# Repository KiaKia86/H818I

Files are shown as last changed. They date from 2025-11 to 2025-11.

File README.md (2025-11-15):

# *H818I*

### A high-performance custom rocket designed entirely from scratch, using a 4-layer avionics PCB, custom airframe, and custom solid motor. The rocket is expected to reach **6,000 ft (≈1,829 m)** at **Mach 0.6**, powered by a **385 N thrust** motor.

### The airframe is constructed with lightweight composite sections reinforced with fiberglass cloth and resin. The rocket includes 2 pyro channels, offering flexibility for multiple deployments and different control configurations.

### The avionics is built on a **4-layer PCB** with one microcontrollers — a **ESP32-S3** — working to process flight data and transmit telemetry via **LoRa** to the ground station. The board includes multiple sensors to track acceleration, rotation, altitude, and GPS position.



---

# Bill of Materials (BOM)

| **Category** | **Item** | **Details** | **Est. Price** | **Purchase Link** |
|---|---|---|---|---|
| Structure | Fiberglass Cloth (6oz) | $21.99 |  | https://www.amazon.com/Fiberglass-Fabric-Glass-Repair-Surfboard/dp/B0DN5FFPSV |
| Structure | Fiberglass Cloth (4oz) | $42.99 |  | https://www.amazon.com/YIQUEDOK-Fiberglass-48-75-Sq-Ft-Surfboard-Repair/dp/B0F74917P7 |
| Structure | Econostitch Peel (5 yards) | $29.95 |  | https://www.amazon.com/Fibre-Glast-Econostitch-Package-Visible/dp/B07DP3PNPJ |
| Structure | TotalBoat 5:1 Marine Epoxy | $159.99 |  | https://www.amazon.com/TotalBoat-Epoxy-Quart-Fast-Hardener/dp/B00HR85152 |
| Structure | Primer | $7.97 |  | https://www.amazon.com/Rust-Oleum-Automotive-260510-12-Ounce-Sandable/dp/B006ZLQ4HQ |
| Structure | Paint | $6.19 |  | https://www.amazon.com/Rust-Oleum-249127-Painters-Purpose-12-Ounce/dp/B002BWOS7Q |
| Structure | Plastic Drop Cloth | $9.47 |  | https://www.amazon.com/Plastic-Drop-Cloths-6-Pack-Disposable/dp/B0DQDWV1SV |
| Structure | Parachute (36 inch) | $18.69 |  | https://www.apogeerockets.com/Building-Supplies/Parachutes/Larger-than-24in/36in-Printed-Nylon-Parachute/Review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 |
| Structure | Kevlar Shock Cord | $40.69 |  | https://www.apogeerockets.com/Building-Supplies/Shock-Cord/Kevlar-Shock-Cord-4500-20-feet-long-3-loops |
| Avionics |PCBA Shipping Cost | $42.22 |  | N/A Custom Quote |

**Total Estimated Cost: $380.15

**Note:**
The PCB cost is not included in the bom, as it is funded by an external source (JLCPCB). Filament and other materials on hand are not considered either!

---

### PCB Overview

The **4-layer PCB** serves as the core of the H818I flight computer.  
It uses:
- **ESP32-S3** (Telemetry, communication, logging, and sensor data)  
- **LoRa radio module** for long-range ground communication  
- Multiple onboard sensors: **IMU**, **barometer**, **magnetometer**, **GPS**, and **accelerometer**  
- **Two pyro channels** for deployment   

The avionics system is designed for flexibility, allowing reuse across future rocket designs.




---

### Why Did I Make This Rocket?

I've wanted to design something that combines all of my passions into one project, and this is it. H818I represents months of hard work, simulation, and testing. Everything I learned about propulsion, control, and flight dynamics has been combined into a single rocket! 

---

# Physical Build
Coming soon!

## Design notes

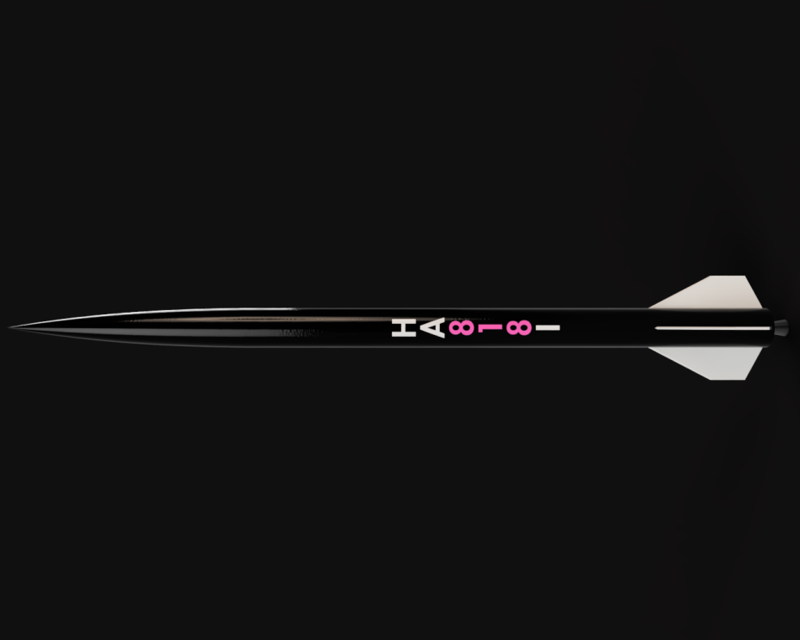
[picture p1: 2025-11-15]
Images/CAD/MainSide1 (1).png

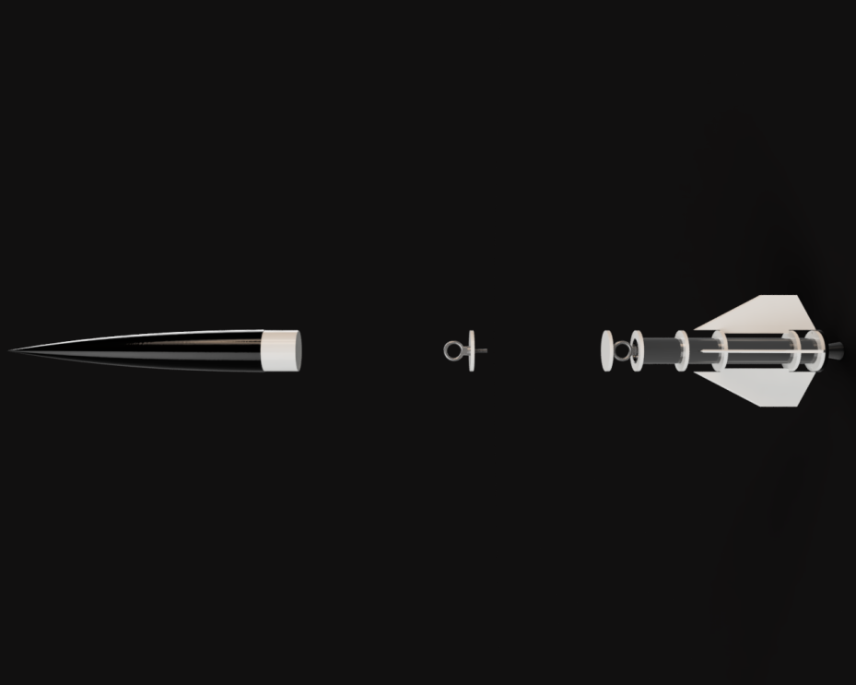
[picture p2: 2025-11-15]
Images/CAD/MainSide2 (1).png

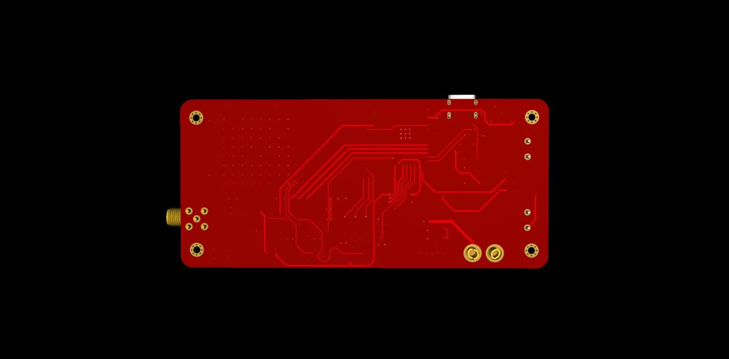
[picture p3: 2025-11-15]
Images/PCB/Screenshot_2025-11-01_200118.png

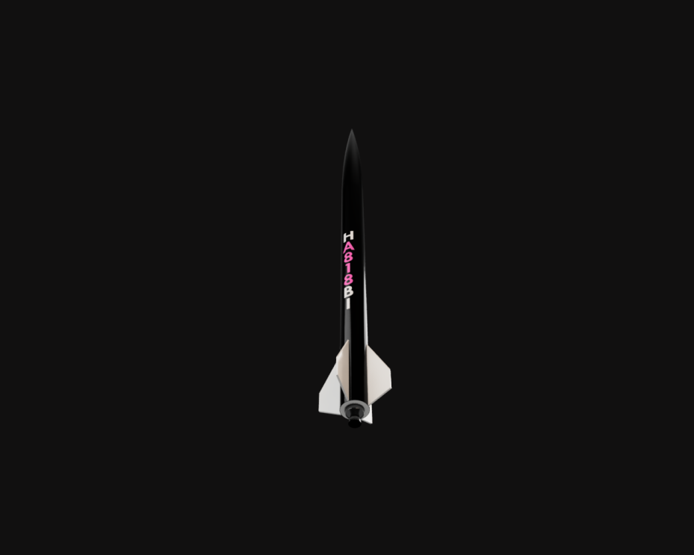
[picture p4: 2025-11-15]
Images/CAD/MainBottomView (1).png

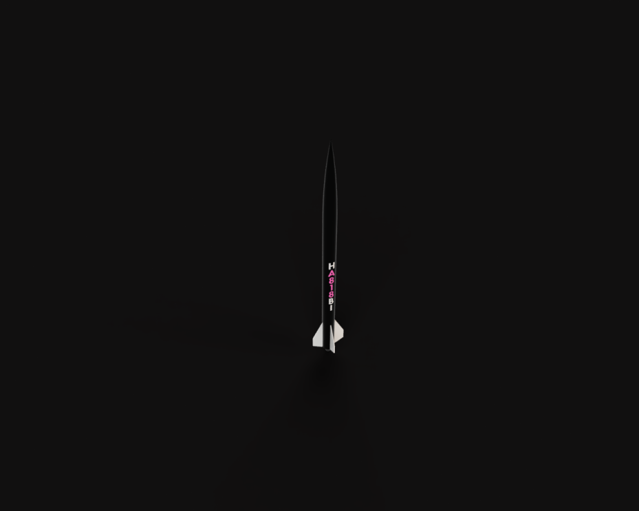
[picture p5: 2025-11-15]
Images/CAD/MainNearView (1).png

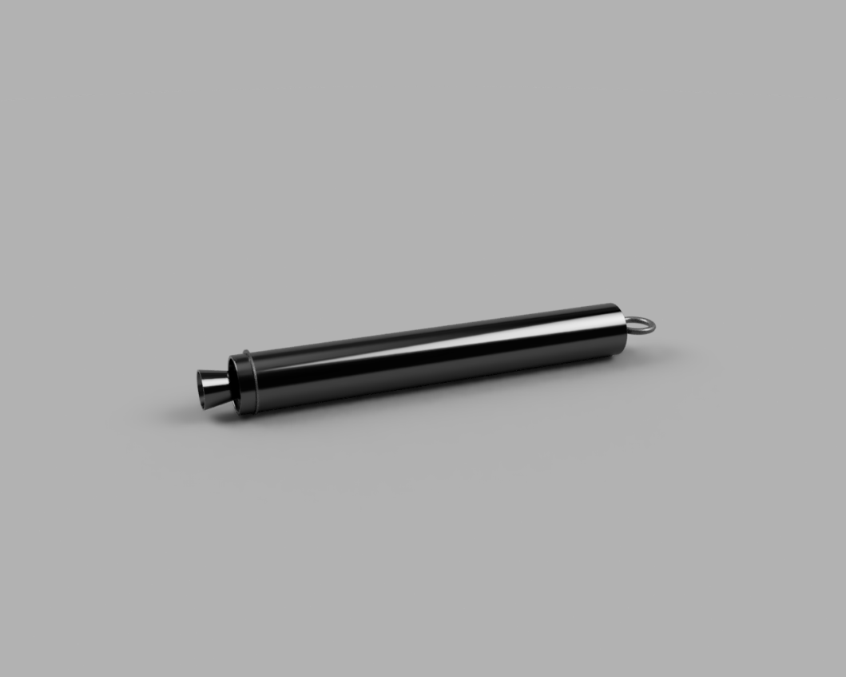
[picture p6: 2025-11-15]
Images/CAD/MainSideRender (1).png

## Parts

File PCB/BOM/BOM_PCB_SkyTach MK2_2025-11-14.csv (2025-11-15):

ID | Name | Designator | Footprint | Quantity | Manufacturer Part | Manufacturer | Supplier | Supplier Part | Price | Pins | 3DModel | Contributor | JLCPCB Part Class | description | license | link
1 | 100nF | C1,C2,C4,C6,C13,C17,C18,C19,C20,C21,C22,C24,C25,C27,C28,C29,C30,C31,C32 | C0603 | 19 | GRM188R71C104KA01D | muRata(村田) | LCSC | C45000 | 0.008 | 2 | C0603_L1.6-W0.8-H0.8 | lcsc | Extended Part |  |  | https://item.szlcsc.com/362304.html
2 | 100nF | C3 | C0603 | 1 | CL10B104KB8NNNC | SAMSUNG(三星) | LCSC | C1591 | 0.003 | 2 | C0603_L1.6-W0.8-H0.8 | lcsc | Extended Part |  |  | https://item.szlcsc.com/362304.html
3 | 1uF | C5 | C0603 | 1 | CL10A105KO8NNNC | SAMSUNG(三星) | LCSC | C1592 | 0.003 | 2 | C0603_L1.6-W0.8-H0.8 | lcsc | Extended Part |  |  | https://item.szlcsc.com/362304.html
4 | 470nF | C12,C15 | C0603 | 2 | GRM188R71A474KA61D | muRata(村田) | LCSC | C435402 | 0.026 | 2 | C0603_L1.6-W0.8-H0.8 | LCSC | Extended Part |  |  | https://item.szlcsc.com/362304.html
5 | 10uF | C23 | C0603 | 1 | C1608X5R1E106MT000E | TDK | LCSC | C76614 | 0.047 | 2 | C0603_L1.6-W0.8-H0.8 | LCSC | Extended Part |  |  | https://item.szlcsc.com/362304.html
6 | 22uF | C7,C8,C9,C10,C11 | C0805 | 5 | GRM21BR61E226ME44L | muRata(村田) | LCSC | C86816 | 0.041 | 2 | C0805_L2.0-W1.3-H1.3 | lcsc | Extended Part |  |  | https://item.szlcsc.com/373011.html
7 | 10uF | C14,C16 | C0805 | 2 | GRM21BR61H106KE43L | muRata(村田) | LCSC | C440198 | 0.063 | 2 | C0805_L2.0-W1.3-H1.3 | LCSC | Basic Part |  |  | https://item.szlcsc.com/373011.html
8 | 1uF | C26 | C0805 | 1 | CL21B105KOFNNNE | SAMSUNG(三星) | LCSC | C24123 | 0.01 | 2 | C0805_L2.0-W1.3-H1.3 | lcsc | Extended Part |  |  | https://item.szlcsc.com/373011.html
9 | TVS | D1,D2,D3 | SOD-523_L1.2-W0.8-LS1.6-BI | 3 | LESD5D5.0CT1G | LRC(乐山无线电) | LCSC | C383211 | 0.021 | 2 | SOD-523_L1.2-W0.8-LS1.6-BI | LCSC | Extended Part |  |  | https://lcsc.com/product-detail/TVS_ESD5Z5V0C_C129211.html
10 | U.FL-R-SMT-1(80) | JP1 | RF-SMD_FRF05002-JSS103M | 1 | U.FL-R-SMT-1(80) | HRS(广濑) | LCSC | C88374 | 0.132 | 3 | RF-SMD_FRF05002-JSS103M | lcsc | Extended Part |  |  | https://atta.szlcsc.com/upload/public/pdf/source/20210518/C2834409_AD8449F4C312B9B9971CC712CA9E2040.pdf
11 | 2.7uH | L1 | IND-SMD_L7.5-W7.5_XAL7030 | 1 | XAL7030-272MEC | Coilcraft(线艺) | LCSC | C5366402 | 1.994 | 2 | IND-SMD_L7.5-W7.5_XAL7030 | lcsc | Extended Part |  |  | https://www.mouser.com/datasheet/2/597/xal7030-270749.pdf
12 | FC-2012HRK-620D | POW | LED0805-R-RD | 1 | NCD0805R1 | 国星光电 | LCSC | C84256 | 0.012 | 2 | LED0805-RD | lcsc | Basic Part |  |  | https://item.szlcsc.com/88042.html
13 | GL | LED2,LED3,LED4 | LED0603-RD | 3 | 19-217/GHC-YR1S2/3T | EVERLIGHT(亿光) | LCSC | C72043 | 0.019 | 2 | LED0603-RD | lcsc | Extended Part |  |  | https://item.szlcsc.com/347874.html
14 | WJ127-5.0-2P | PYRO1,PYRO2 | CONN-TH_2P-P5.00_CPC3703CTR | 2 | WJ127-5.0-2P | KANGNEX(康奈克斯电气) | LCSC | C3703 | 0.129 | 2 | CONN-TH_2P-P5.00_CPC3703CTR | lcsc | Extended Part |  |  | https://item.szlcsc.com/98720.html
15 | SI7232DN-T1-GE3 | Q1 | POWER-1212-8_L3.3-W3.3-P0.66-LS3.3-BL | 1 | SI7232DN-T1-GE3 | VISHAY(威世) | LCSC | C144854 | 0.756 | 10 | POWER-1212-8_L3.3-W3.3-P0.66-LS3.3-BL | LCSC | Extended Part |  |  | https://item.szlcsc.com/152942.html
16 | 10kΩ | R1,R2,R5,R7,R8 | R0603 | 5 | 0603WAJ0103T5E | UNI-ROYAL(厚声) | LCSC | C15401 | 0.001 | 2 | R0603 | lcsc | Extended Part |  |  | https://www.mouser.in/datasheet/2/447/PYu_RT_1_to_0_01_RoHS_L_11-1669912.pdf
17 | 100kΩ | R3 | R0603 | 1 | RC0603FR-07100KL | YAGEO(国巨) | LCSC | C14675 | 0.001 | 2 | R0603 | LCSC | Extended Part |  |  | https://www.mouser.in/datasheet/2/447/PYu_RT_1_to_0_01_RoHS_L_11-1669912.pdf
18 | 100Ω | R11,R12,R15 | R0603 | 3 | RT0603BRD07100RL | YAGEO(国巨) | LCSC | C122970 | 0.02 | 2 | R0603 | lcsc | Extended Part |  |  | https://www.mouser.in/datasheet/2/447/PYu_RT_1_to_0_01_RoHS_L_11-1669912.pdf
19 | 5.1kΩ | R4,R6 | R0805 | 2 | RMC08055.1K1%N | Tyohm(幸亚电阻) | LCSC | C269748 | 0.006 | 2 | R0805_L2.0-W1.3-H0.6 | LCSC | Extended Part |  |  | https://item.szlcsc.com/142685.html
20 | 4.7kΩ | R9,R10,R13,R14 | R0805 | 4 | ERJ6RBD4701V | PANASONIC(松下) | LCSC | C336873 | 0.018 | 2 | R0805_L2.0-W1.3-H0.6 | LCSC | Extended Part |  |  | https://item.szlcsc.com/142685.html
21 | KH-SMA-K513-G | RF1 | ANT-TH_KH-SMA-K513-G | 1 | KH-SMA-K513-G | kinghelm(金航标) | LCSC | C411575 | 0.584 | 5 | ANT-TH_L14.8-W6.4-H10.0 | LCSC | Extended Part |  |  | https://item.szlcsc.com/402832.html
22 | K2-1808SN-A4SW | EN,BOOT | KEY-SMD_4P-L4.2-W3.2-P2.20-LS5.1-TL | 2 | K2-1808SN-A4SW-01 | 韩国韩荣 | LCSC | C92589 | 0.088 | 4 | KEY-SMD_4P-L4.2-W3.2-H2.5-LS5.1-P2.2 | 立创EDA官方封装库 | Extended Part |  |  | https://item.szlcsc.com/157210.html
23 | XT60 | 2S-4S | CONN-TH_XT60 | 1 | XT60-M. | AMASS(艾迈斯) | LCSC | C98733 | 0.363 | 2 | CONN-TH_XT60 | lcsc | Extended Part |  |  | https://atta.szlcsc.com/upload/public/pdf/source/20170606/1496716524919.pdf
24 | AP2114H-3.3TRG1 | 3.3V_LDO | SOT-223_L6.7-W3.5-P2.30-BR | 1 | AP2114H-3.3TRG1 | DIODES(美台) | LCSC | C150716 | 0.123 | 4 | SOT-223-4P_L6.5-W3.5-H1.6-LS7.0-P2.30 | LCSC | Extended Part |  |  | https://item.szlcsc.com/245102.html
25 | LM61495Q5RPHRQ1_C3188409 | REG | VQFN-16_L4.5-W3.5-P0.50-TL_TI_RPH | 1 | LM61495Q5RPHRQ1 | TI(德州仪器) | LCSC | C3188409 | 5.233 | 16 | VQFN-16_L4.5-W3.5-P0.50-TL_TI_RPH | lcsc | Extended Part |  |  | https://www.ti.com/cn/lit/ds/symlink/lm61495-q1.pdf?ts=1646269284230
26 | ESP32-S3-WROOM-1U-N16 | ESP32-S3 | WIRELM-SMD_ESP32-S3-WROOM-1U | 1 | ESP32-S3-WROOM-1U-N16 | ESPRESSIF(乐鑫) | LCSC | C2980298 | 5.257 | 49 | WIRELM-SMD_ESP32-S3-WROOM-1U | LCSC | Extended Part |  |  | https://www.mouser.cn/datasheet/2/891/Espressif_ESP32_S3_WROOM_1_1U_Preliminary-2530171.pdf
27 | MAX-M8Q-0 | MAX-M8Q-0 | COMM-SMD_MAX-M8Q-0 | 1 | MAX-M8Q-0 | U-BLOX | LCSC | C6898733 | 6.373 | 18 | COMM-SMD_MAX-M8Q-0 | lcsc | Extended Part |  |  | https://content.u-blox.com/sites/default/files/documents/MAX-M8-FW3_DataSheet_UBX-15031506.pdf
28 | H3LIS331DLTR | ACC | LGA-16_L3.0-W3.0-P0.50-BL | 1 | H3LIS331DLTR | ST(意法半导体) | LCSC | C2655074 | 10.815 | 16 | LGA-16_L3.0-W3.0-P0.50-TL | LCSC | Extended Part |  |  | https://atta.szlcsc.com/upload/public/pdf/source/20210630/1C9F4EDC238703964D614E96D02F8129.pdf
29 | IAM-20680HT_C3288649 | 20680HT | LGA-16_L3.0-W3.0-P0.50-BL | 1 | IAM-20680HT | TDK InvenSense(应美盛) | LCSC | C3288649 | 5.309 | 16 | LGA-16_L3.0-W3.0-P0.50-TL | lcsc | Extended Part |  |  | https://atta.szlcsc.com/upload/public/pdf/source/20210630/1C9F4EDC238703964D614E96D02F8129.pdf
30 | E22-400T37S | E22-400T37S | WIRELM-SMD_E22-400T37S | 1 | E22-400T37S | EBYTE(亿佰特) | LCSC | C5844211 | 42.832 | 85 |  | lcsc | Extended Part |  |  | https://atta.szlcsc.com/upload/public/pdf/source/20230506/B71D51EBD6DC7750D26C230FFB0B75CE.pdf
31 | GND | GND,GND,GND,GND | MOUNTINGHOLE_2.2MM_M2_PAD_VIA | 4 |  |  |  |  |  | 9 |  | Nazar D Plus |  |  | https://www.gnu.org/licenses/lgpl-2.1.html
32 | LIS3MDLTR | LIS3MDLTR | LGA-12_L2.0-W2.0-P0.50-BL | 1 | LIS3MDLTR | ST(意法半导体) | LCSC | C478483 | 3.639 | 12 | LGA-12_L2.0-W2.0-H1.0-P0.50 | LCSC | Extended Part | LGA-12 2x2x1 mm 12-lead |  | https://so.szlcsc.com/global.html?c=&k=C915682
33 | AHT20 | AHT20 | DFN-6_L3.0-W3.0-P1.00-BL | 1 | AHT20 | 广州奥松 | LCSC | C503357 |  | 6 | DFN-6_L3.0-W3.0-P1.00-BL | LCSC | Extended Part |  |  | https://item.szlcsc.com/515997.html
34 | BMP390_C5124834 | BMP390 | LGA-10_L2.0-W2.0-P0.50-BL | 1 | BMP390 | Bosch(博世) | LCSC | C5124834 | 3.458 | 10 | LGA-10_L2.0-W2.0-P0.50-BL | lcsc | Extended Part |  |  | https://img.jlc.com/pdf/applyPasteComponent/2022-03-15/213669K/16defc8df665443c85df0cd6383d7c1b/BMP384.pdf
35 | CY15B104Q-SXI | FRAM | SOIC-8_L5.2-W5.2-P1.27-LS8.0-BL | 1 | CY15B104Q-SXI | Infineon/CYPRESS(赛普拉斯) | LCSC | C2759922 | 15.651 | 8 | SOIC-8_L5.2-W5.2-P1.27-LS8.0-BL | LCSC | Extended Part |  |  | https://atta.szlcsc.com/upload/public/pdf/source/20180713/C94222_E9393EDE83A8A913A4D73B03C6220040.pdf
36 | HC-TYPE-C-16P-01A-G | USB1 | USB-C-SMD_G-SWITCH_GT-USB-7010EN | 1 | HC-TYPE-C-16P-01A-G | HCTL(华灿天禄) | LCSC | C2997435 | 0.165 | 16 | USB-C-SMD_G-SWITCH_GT-USB-7010EN | lcsc | Extended Part |  |  | https://atta.szlcsc.com/upload/public/pdf/source/20220429/DBF6CF34305C712BCF88AF8C50C2E7F9.pdf

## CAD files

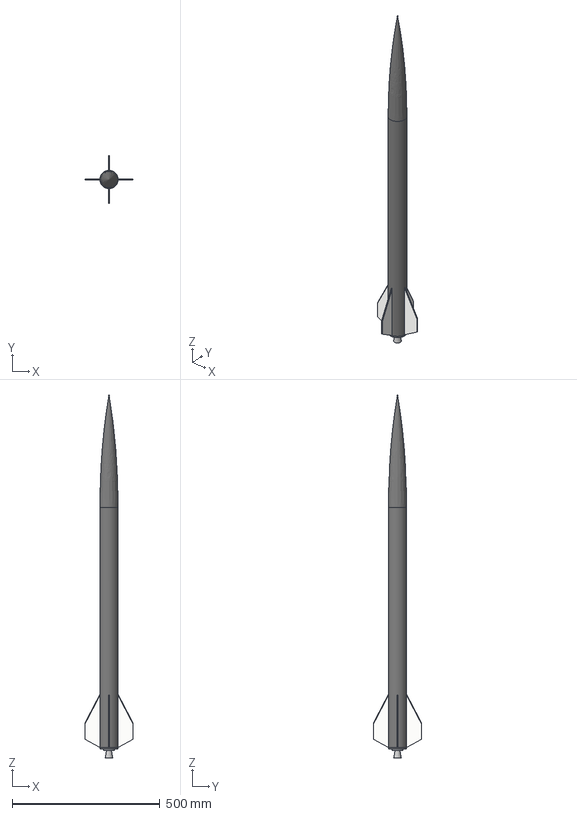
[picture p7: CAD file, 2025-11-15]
CAD/Airframe/STEP/AssembledRocket(Avionics)_.step
164.0 x 164.0 x 1229.8 mm
Tube
Nozzle
Forward Closure
O-Ring (9452K35) x 2
Retaining Ring (98409A232) x 2
Spiral Retaining Ring (91650A510)
38mm Tube Liner
Propellant With Case (2.25 H/0.5 ID/1.212 OD) x 4
Eyebolt (3014T45) x 2
Body Tube
Motor Retainer x 4
Lower Fin
Motor Holder
Motor Holder Mount
18650_cell x 2
GPS
2.4 GHz Antenna Base
2.4 GHz Antenna Top

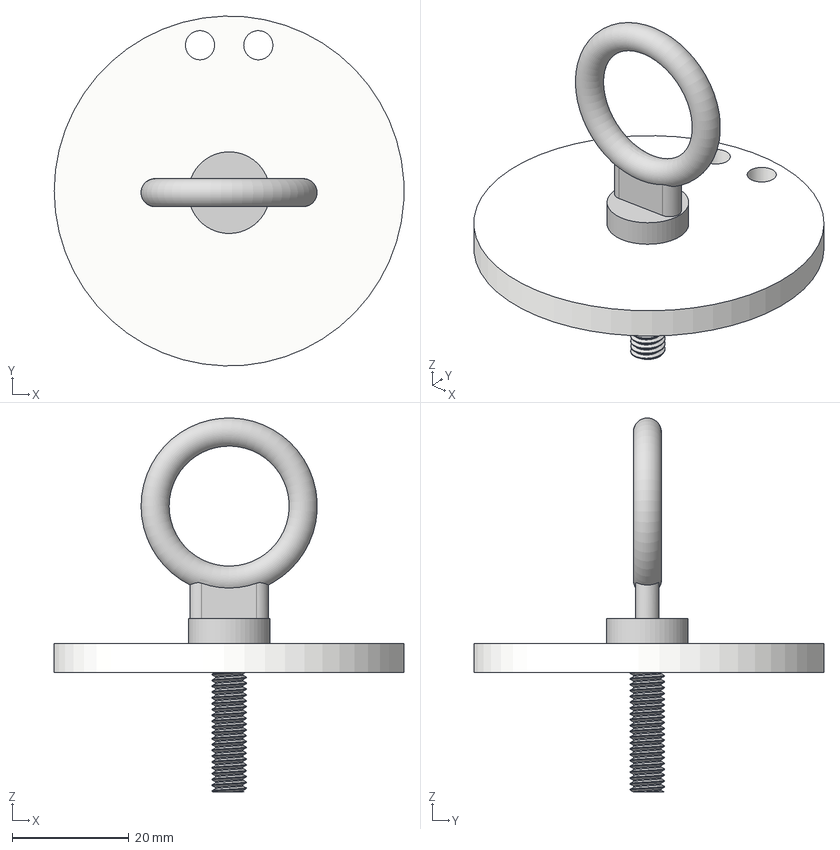
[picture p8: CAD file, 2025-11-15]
CAD/Airframe/STEP/Forward Bulk Head.step
59.9 x 60.0 x 64.1 mm

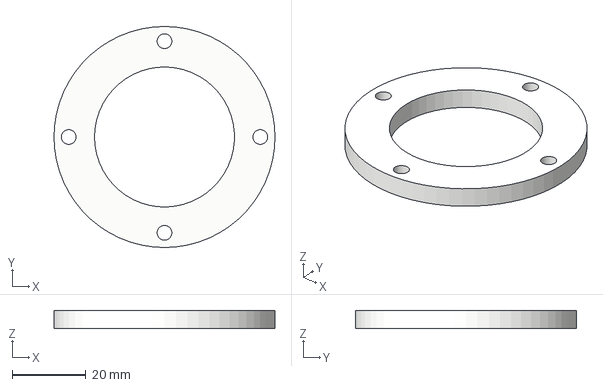
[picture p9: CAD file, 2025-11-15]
CAD/Airframe/STEP/Motor Holder Mount.step
60.0 x 60.0 x 5.00 mm

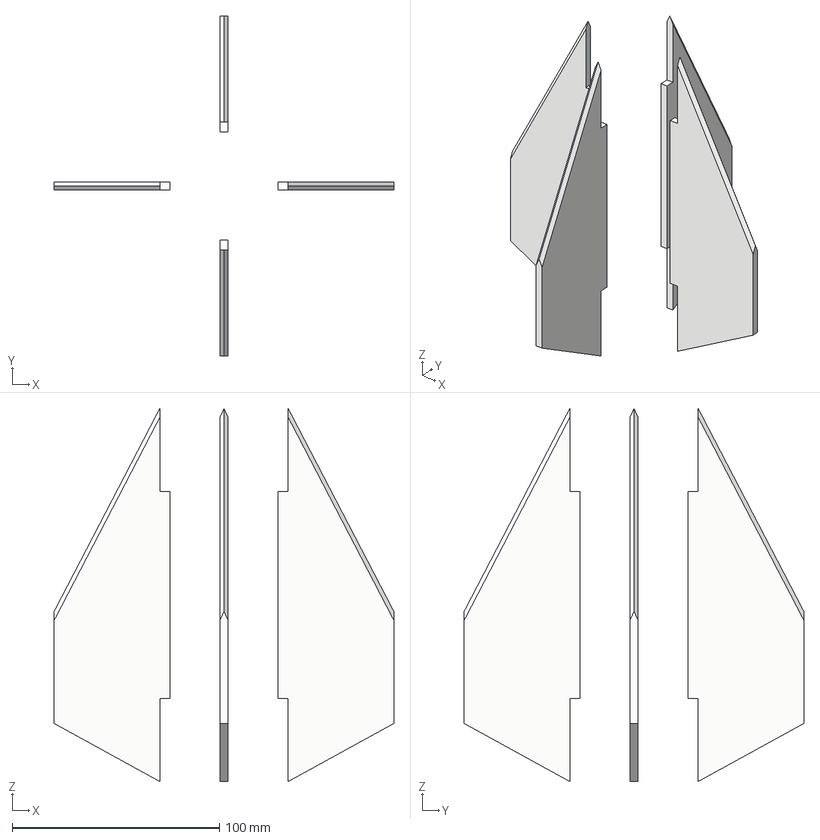
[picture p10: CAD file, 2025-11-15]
CAD/Airframe/STEP/Lower Fin.step
164.0 x 164.0 x 180.0 mm

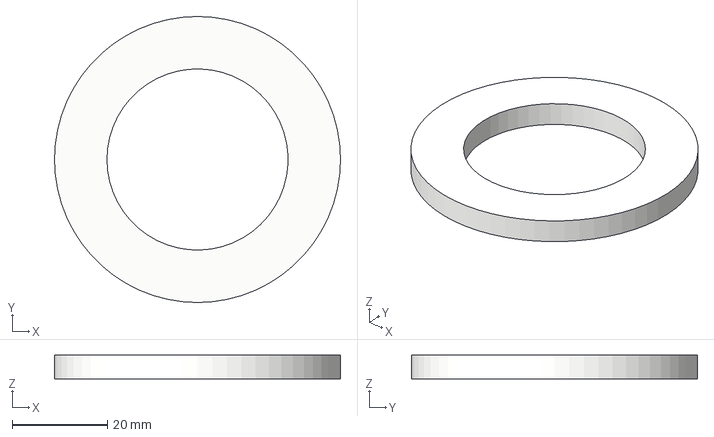
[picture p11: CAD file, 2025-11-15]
CAD/Airframe/STEP/Motor Retainer.step
60.0 x 60.0 x 5.00 mm

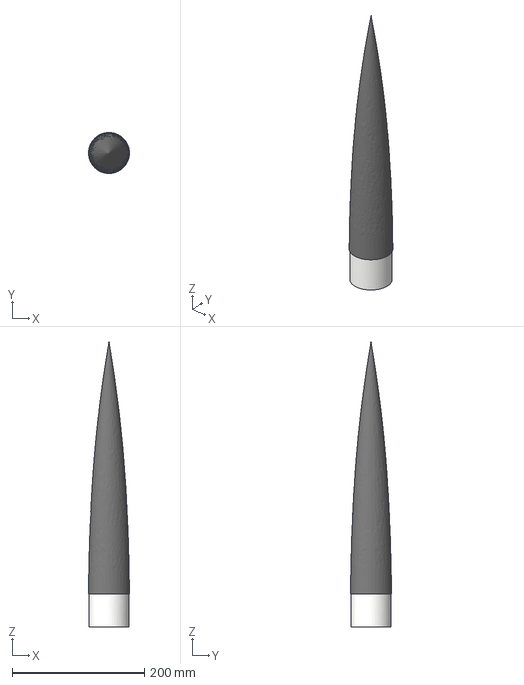
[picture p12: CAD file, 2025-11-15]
CAD/Airframe/STEP/Nose Cone_.step
61.9 x 62.0 x 431.0 mm

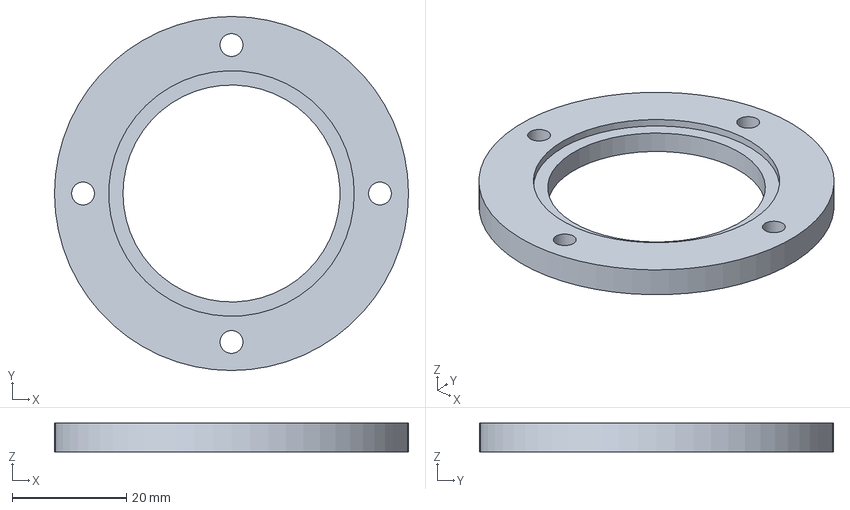
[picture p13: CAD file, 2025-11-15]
CAD/Airframe/STEP/Motor Holder.step
62.0 x 62.0 x 5.00 mm

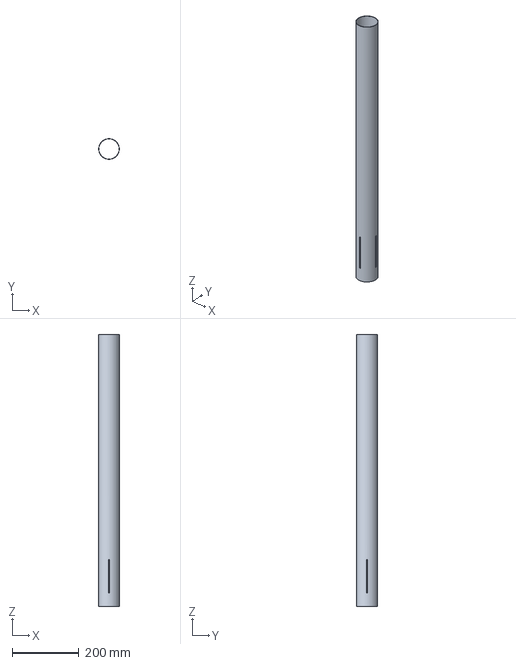
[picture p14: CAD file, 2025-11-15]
CAD/Airframe/STEP/Body Tube.step
62.0 x 62.0 x 813.0 mm

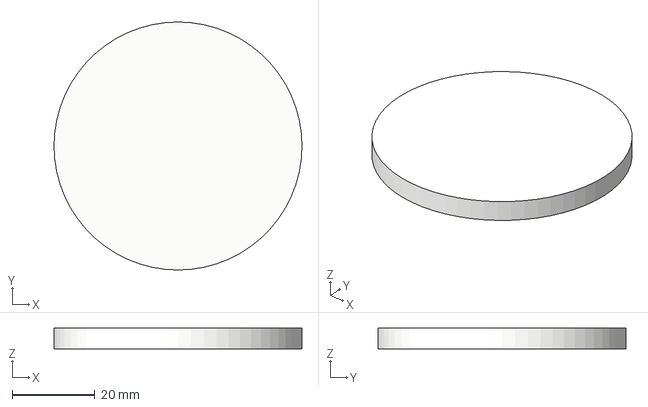
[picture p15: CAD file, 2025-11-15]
CAD/Airframe/STEP/Bulkhead.step
60.0 x 60.0 x 5.00 mm

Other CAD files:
CAD/Airframe/STL/Body Tube.stl
CAD/Airframe/STL/Bulkhead.stl
CAD/Airframe/STL/Forward Bulk Head.stl
CAD/Airframe/STL/Lower Fin.stl
CAD/Airframe/STL/Motor Holder Mount.stl
CAD/Airframe/STL/Motor Holder_.stl
CAD/Airframe/STL/Motor Retainer.stl
CAD/Airframe/STL/Nose Cone.stl

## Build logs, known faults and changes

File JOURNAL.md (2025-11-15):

| Title | Author | Description | Created_at |
|---|---|---|---|
| H818I | Kiya | A high-performance custom rocket with full avionics, airframe, and motor designed from scratch. | 2025-10-02 |

# Dev Log "H818I"

**Total Time (Hours): 42 Hours**

---

## Week 1 (10/02/2025) – 8 Hours  

**Days worked on:**  
Thursday – 2 hours<br>
Friday – 1 hour<br>
Saturday – 3 hours<br>
Sunday – 2 hours  

- Started to plan the rocket
- Created an open rocket simulation to predict how fast the rocket would go
- Made sketches and a model (Very rough) to get an idea of what the rocket would look like 
- Researched materials for motor (304 steel and 6061 aluminum)
- Modeled nose cone and body tube in Fusion 360

**Open Rocket Simulation**

**Body Tube**

**Nose Cone**


---

## Week 2 (10/09/2025) – 10 Hours  

**Days worked on:**  
Monday – 2 hours<br>
Tuesday – 2 hours<br>
Wednesday – 3 hours<br>
Thursday – 2 hours<br>
Friday – 1 hour  

- Designed the finalized the motor size (38mm x 277mm, with 385N of thrust) 
- Modeled grain holders  
- Started designing 4-layer avionics PCB  
- Designed fins based on the openrocket simulation and data  
- Confirmed center of gravity and stability margin through simulations

**Full Motor Design**

**Motor Cross Section**

**Propellant Case Mold**

**Fins**


---

## Week 3 (10/16/2025) – 9 Hours  

**Days worked on:**  
Monday – 2 hours<br>
Tuesday – 1 hour<br>
Wednesday – 3 hours<br>
Thursday – 2 hours<br>
Friday – 1 hour  

- Started and finished the schematic for the flight controller
- Added two pyro channels for deployment
- Designed the bulkheads of the rocket
- Started PCB layout using the SGGS rule (EMI protection)
  
**PCB schematic**

**Motor retainers and bulkheads**

**Pyro Channels**


---

## Week 4 (10/23/2025) – 8 Hours  

**Days worked on:**  
Monday – 1 hour<br>
Tuesday – 2 hours<br>
Wednesday – 2 hours<br>
Thursday – 1 hour<br>
Friday – 2 hours  

- Finished the PCB layout with optimization
- Double-checked all wiring
- Checked design rule, and everything looked good
- Started to download libraries in preparation for the PCBs

**PCB Layout**


---

## Week 5 (10/30/2025) – 7 Hours  

**Days worked on:**  
Monday – 1 hour<br>
Tuesday – 2 hours<br>
Wednesday – 1 hour<br>
Thursday – 2 hours<br>
Friday – 1 hour  

- Designed avionics enclosure
- Added 2s battery support
- Researched composites and practiced with friends
- Researched things needed for recovery
- Optimized BOM 

**Avionics Bay**


---
